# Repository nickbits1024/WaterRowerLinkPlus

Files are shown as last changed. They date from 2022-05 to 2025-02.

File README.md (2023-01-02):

# WaterRower Link+

## Description
WaterRower Link+ is a bluetooth module designed for any WaterRower with the S4 monitor.  It provides all the functionality of the official WaterRower ComModule as well as many additional features.

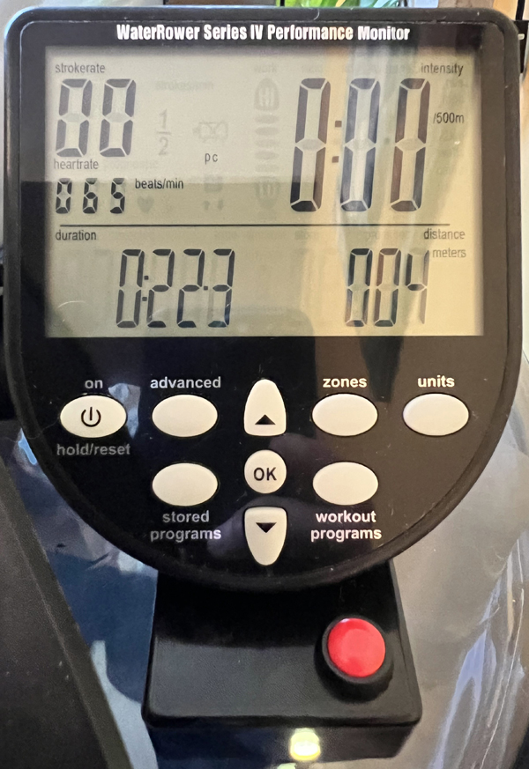
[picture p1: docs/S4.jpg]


## Features
- Replaces WaterRower ComModule and External ANT+ Module
  - External ANT+ connection Works on M1 when using recommended cable (unlike the official ANT+ Plugin-In module!)
- Bluetooth
  - Bluetooth Fitness Machine Profile
    - Rower Data
    - Indoor Bike Data
  - Supports BLE HRMs
- ANT+
  - Fitness Equipment Profile
  - Supports ANT+ HRMs
- S4 monitor heart rate provider
  - Sends captured ANT+/BLE HR data for display on S4 monitor
- ANT+ to BLE HRM bridge
  - WRL+ will broadcast ANT+ HR data over BLE for use in apps that only support BLE. e.g. SuperNatural

## Tested Software
- WaterRower Connect
- Holofit
- VZFit
- ZWift
- Garmin Fenix 6
- SuperNatural (HR only)

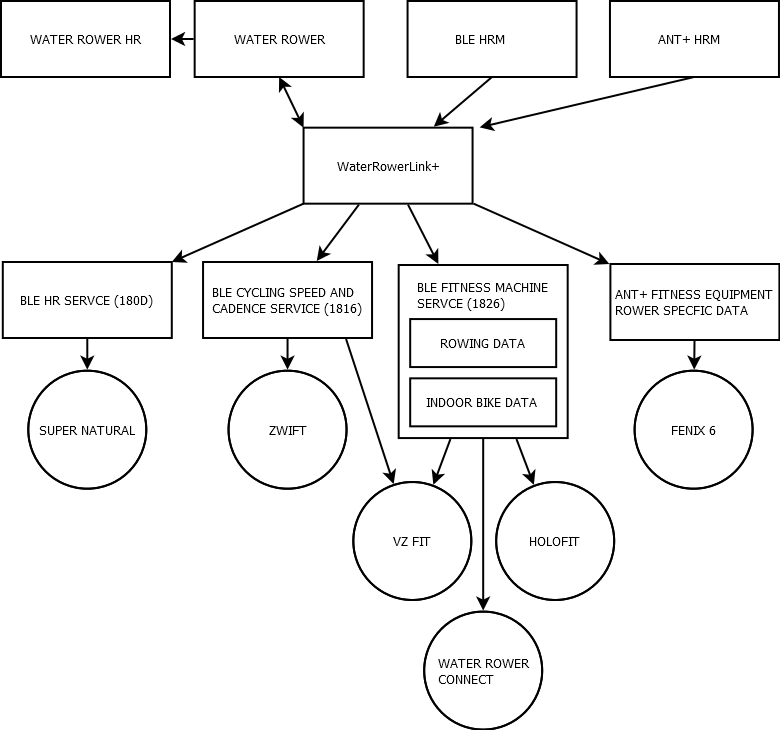
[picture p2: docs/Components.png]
Components


## Hardware
Hardware design is available in the KiCad projects in this repo.  There are two versions, [breadboard](hardware/breadboard/) and [PCB](hardware/pcb/).  With the breadboard version, everything can be assembled using dev boards and jumper wires. [^1]  Both solderless and soldered breadboards were tested and work.  The PCB version requires the design be sent to a PCB manufacturer.

### Soldered Breadboard Version
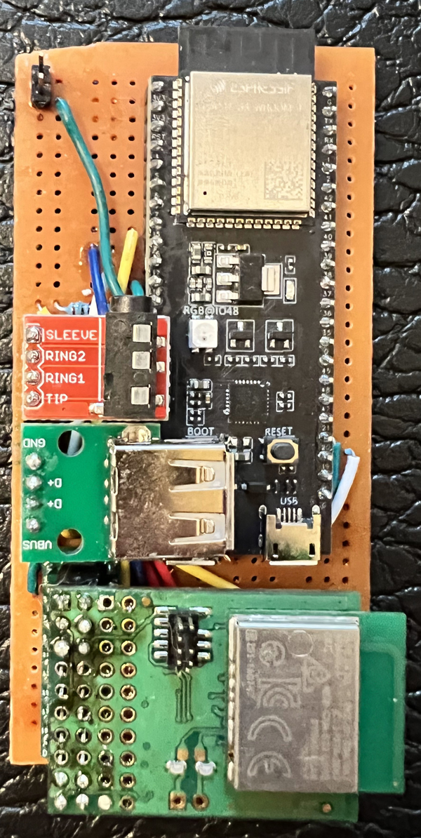
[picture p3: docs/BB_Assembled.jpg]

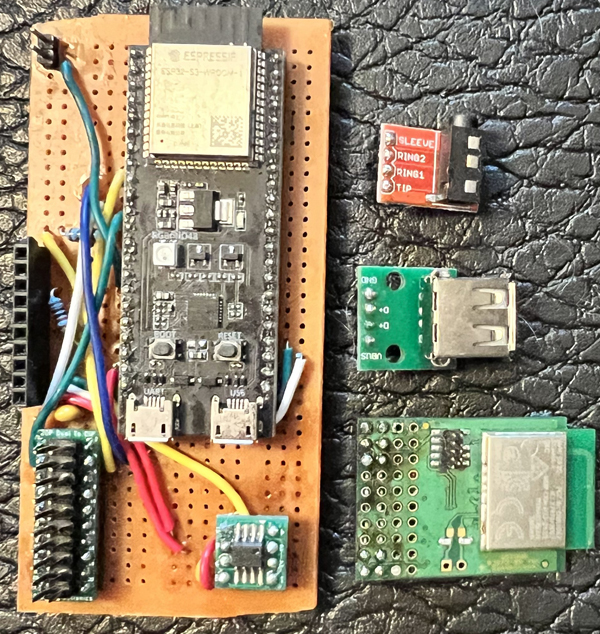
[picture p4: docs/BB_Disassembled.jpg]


### PCB Version
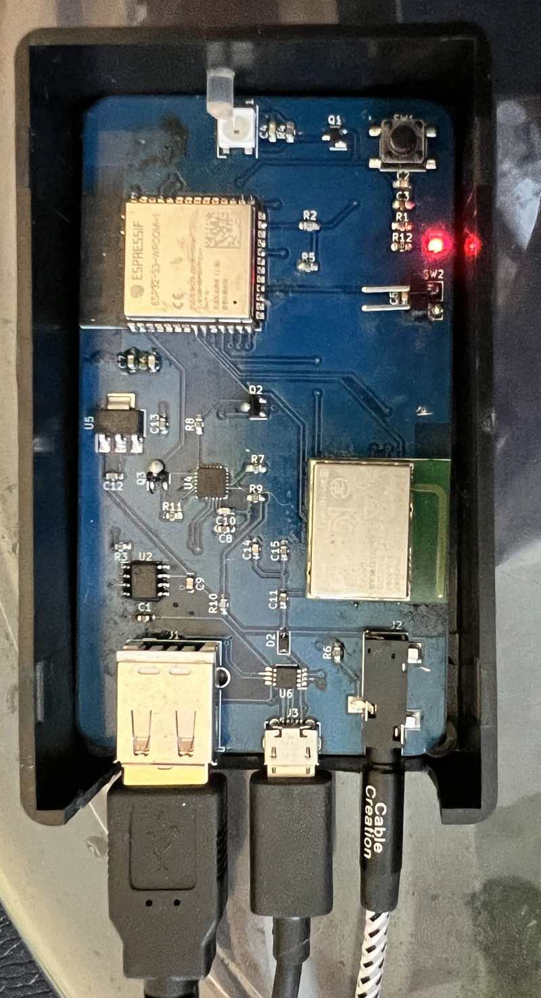
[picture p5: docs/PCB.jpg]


## Breadboard Bill of Materials
|Qty|Reference|Part|Foot Print|Supplier|
|---|---|----|---|---|
|1|C1|1uF|THT||[Amazon](https://www.amazon.com/gp/product/B085RDTCCV)
|1|C2|0.1uF|THT||(See above)
|1|J1|AudioPlug3|2.54mm|[Amazon](https://www.amazon.com/gp/product/B07L3P93ZD)
|1|J4|USB_A|2.54mm|[Amazon](https://www.amazon.com/gp/product/B07MBSTZYG)
|2|R1, R2|10k|THT|[Amazon](https://www.amazon.com/gp/product/B072BL2VX1)
|1|SW2|Button|12mm|[Amazon](https://www.amazon.com/gp/product/B07F8GBWGG)
|1|U1|ESP32-S3-DevKitC-1|DIP|[Amazon](https://www.amazon.com/gp/product/B09CPNRDND)
|1|U2|LM3525M-H|SOIC-8|[Mouser](https://www.mouser.com/ProductDetail/926-LM3525MX-H-NOPB)
|1|U2|SOIC-8 TO DIP||[Amazon](https://www.amazon.com/gp/product/B07CJ96ZPW)
|1|U3|D52QD2M6IA[^2]|2x10_2.54mm|[Digi-Key](https://www.digikey.com/en/products/detail/garmin-canada-inc/D52QD2M6IA-A-TRAY/6149453)
|1||PCB Breadboard|50x100|[Amazon](https://www.amazon.com/gp/product/B07ZP4FYVJ)
|1|Project Box|B07W78LN1V|100 x 60 x 25|[Amazon](https://www.amazon.com/gp/product/B07W78LN1V)
|1|TRS Cable|CC0377|3.5mm|[Amazon](https://www.amazon.com/gp/product/B01K3WXQDW)
|1|USB Cable|3896|Mini USB|[Monoprice](https://www.monoprice.com/product?p_id=3896)

## PCB Bill of Materials
|Qty|Reference|Part|Foot Print|Supplier|
|---|---|----|---|---|
|2|C1, C3|1uF cap|0603|[Amazon](https://www.amazon.com/gp/product/B06XDG3WQX)
|8|C2, C4, C5, C6, C9, C10, C14, C16|0.1uF cap|0603|(See above)
|2|C7, C11|C 10uF cap|0603|(See above)
|4|C8, C12, C13, C15|4.7uF cap|0603|(See above)
|1|D1|SK6812|5x5mm|[Digi-Key](https://www.digikey.com/en/products/detail/adafruit-industries-llc/1655/5154679)
|1|D2|1N5819|SOD-323|[Digi-Key](https://www.digikey.com/en/products/detail/micro-commercial-co/B5819WS-TP/2213555)
|1|D3|RED LED|0603|[Amazon](https://www.amazon.com/gp/product/B01CUGA380)
|1|J1|Molex_67643|USB-A|[Mouser](https://www.mouser.com/ProductDetail/538-67643-3910)
|1|J2|CUI_SJ-3523|3.5mm|[Mouser](https://www.mouser.com/ProductDetail/490-SJ-3523-SMT-TR)
|1|J3|Molex-105017-0001|Micro USB|[Mouser](https://www.mouser.com/ProductDetail/538-105017-0001)
|1|Q1|BSS138|SOT-23|[Mouser](https://www.mouser.com/ProductDetail/512-BSS138W)
|2|Q2, Q3|S8050|SOT-23|[Amazon](https://www.amazon.com/gp/product/B07KPCBP24)
|7|R1, R3, R4, R5, R6, R8, R11|10K res|0603|[Amazon](https://www.amazon.com/gp/product/B095P6L5PB)
|2|R2, R7|1K res|0603|(See above)
|1|R9|47K res|0603|(See above)
|1|R10|22K res|0603|(See above)
|1|R12|5.1K res|0603|(See above)
|1|SW2|Header|2x2.54mm|[Amazon](https://www.amazon.com/gp/product/B01461DQ6S) 
|1|SW2|Button|12mm|[Amazon](https://www.amazon.com/gp/product/B07F8GBWGG)
|1|SW4|RESET|2x2.54mm|(See above)
|1|SW1|RESET|6x6mm|[Amazon](https://www.amazon.com/gp/product/B077N3D7BD)
|1|SW3|BOOT|6x6mm|(See RESET)
|1|U1|ESP32-S3-WROOM-1|ESP32-S3-WROOM-1|[Mouser](https://www.mouser.com/ProductDetail/356-ESP32-S3WROOM1N8)
|1|U2|LM3525M-H|SOIC-8|[Mouser](https://www.mouser.com/ProductDetail/926-LM3525MX-H-NOPB)
|1|U3|D52Q|D52QD2M4IA|[Digi-Key](https://www.digikey.com/en/products/detail/garmin-canada-inc/D52QD2M4IA-TRAY/6149451)
|1|U4|CP2102N-Axx-xQFN24|QFN-24|[Digi-Key](https://www.digikey.com/en/products/detail/silicon-labs/CP2102N-A02-GQFN24/9863476)
|1|U5|AP7361C-33E|SOT-223|[Digi-Key](https://www.digikey.com/en/products/detail/diodes-incorporated/AP7361-33E-13/4249788)
|1|U6|SP0506BAATG|MSOP-8|[Mouser](https://www.mouser.com/ProductDetail/576-SP0506BAATG)
|1|Project Box|B07W78LN1V|100 x 60 x 25|[Amazon](https://www.amazon.com/gp/product/B07W78LN1V)
|1|TRS Cable|CC0377|3.5mm|[Amazon](https://www.amazon.com/gp/product/B01K3WXQDW)
|1|USB Cable|3896|Mini USB|[Monoprice](https://www.monoprice.com/product?p_id=3896)
|1|Light Pipe||RA|[Digi-Key](https://www.digikey.com/en/products/detail/dialight/51513620375F/9742144)

## Cable Connections
1. Attach mini USB cable to S4 monitor and WaterRower Link+
2. Attach 3.5mm cable to S4 monitor and WaterRower Link+.  The recommended cable will fit in the narrow gap of an M1 rower and the monitor.
2. Attach micro USB cable to USB power supply

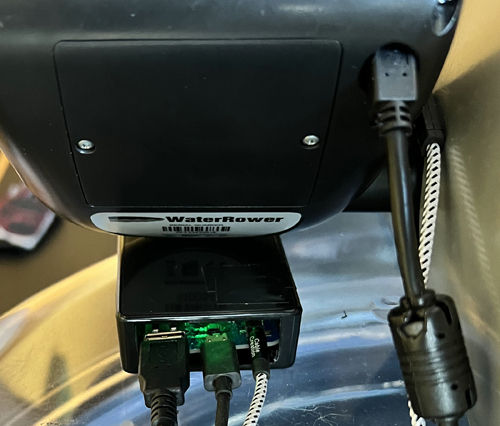
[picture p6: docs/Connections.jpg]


### Required Software
- [Visual Studio Code](https://code.visualstudio.com/download)
- [Visual Studio Code Espressif IDF extension](https://marketplace.visualstudio.com/items?itemName=espressif.esp-idf-extension)
- [ESP-IDF](https://dl.espressif.com/dl/esp-idf/) Built using commit 0132079fa51f2c130513dd634e97ef9726f00e85

### Equipment Used
- Soldering Iron: [YIHUA 995D+](https://www.amazon.com/gp/product/B0919MS875)
- PCB Hot Plate: [MINIWARE MHP30M Mini Hot Plate](https://www.amazon.com/gp/product/B08R6XFPKR)
- PCB Holder: [Stickvise](https://www.stickvise.com/)
- Microscope: [AMScope SM745NTP-B](https://amscope.com/products/sm745ntp-b) + [DAB](https://amscope.com/products/DAB)

## Usage
Once power is provided, a red LED will illuminate on the board and should be detectable in apps.  Press the button connected to SW2 turn on the S4 monitor.  The NeoPixel will illuminate green when it detects it over the USB connection.  It will power off automatically after 30 minutes of inactivity.  When WRL+ is receiving data from the S4, the LED will turn cyan. When it detects a heart rate over BLE or ANT+, it will beat red.
Note the software only supports one HRM.  If multiple are detected, only the first one seen will be connected.

## Known Issues
- The last update to VZfit displays HR in the HUD however the value does not appear correct.  It may be a bug with WRL+ or VZfit.

## Credits
This project was inspired by [PiRowFlow](https://github.com/inonoob/pirowflo)

[^1]: The LM3525M must be soldered to the SOIC-8 TO DIP first
[^2]: This part is EOL at Digi-Key.  I do not know if there is a compatible replacement.

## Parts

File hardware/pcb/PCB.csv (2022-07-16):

Source: | C:\Users\nickb\Documents\esp-idf\WaterRowerLinkPlus\hardware\PCB\PCB.kicad_sch
Date: | 7/16/2022 12:26:23 PM
Tool: | Eeschema (6.0.5)
Generator: | C:\Program Files\KiCad\6.0\bin\scripting\plugins/bom_csv_grouped_by_value.py
Component Count: | 47
Individual Components:
Item | Qty | Reference(s) | Value | LibPart | Footprint | Datasheet
 |  | C1 | 1uF | Device:C | Capacitor_SMD:C_0603_1608Metric_Pad1.08x0.95mm_HandSolder | ~
 |  | C2 | 0.1uF | Device:C | Capacitor_SMD:C_0603_1608Metric_Pad1.08x0.95mm_HandSolder | ~
 |  | C3 | 1uF | Device:C | Capacitor_SMD:C_0603_1608Metric_Pad1.08x0.95mm_HandSolder | ~
 |  | C4 | 0.1uF | Device:C | Capacitor_SMD:C_0603_1608Metric_Pad1.08x0.95mm_HandSolder | ~
 |  | C5 | 0.1uF | Device:C | Capacitor_SMD:C_0603_1608Metric_Pad1.08x0.95mm_HandSolder | ~
 |  | C6 | 0.1uF | Device:C | Capacitor_SMD:C_0603_1608Metric_Pad1.08x0.95mm_HandSolder | ~
 |  | C7 | 10uF | Device:C | Capacitor_SMD:C_0603_1608Metric_Pad1.08x0.95mm_HandSolder | ~
 |  | C8 | 4.7uF | Device:C | Capacitor_SMD:C_0603_1608Metric_Pad1.08x0.95mm_HandSolder | ~
 |  | C9 | 0.1uF | Device:C | Capacitor_SMD:C_0603_1608Metric_Pad1.08x0.95mm_HandSolder | ~
 |  | C10 | 0.1uF | Device:C | Capacitor_SMD:C_0603_1608Metric_Pad1.08x0.95mm_HandSolder | ~
 |  | C11 | 10uF | Device:C | Capacitor_SMD:C_0603_1608Metric_Pad1.08x0.95mm_HandSolder | ~
 |  | C12 | 4.7uF | Device:C | Capacitor_SMD:C_0603_1608Metric_Pad1.08x0.95mm_HandSolder | ~
 |  | C13 | 4.7uF | Device:C | Capacitor_SMD:C_0603_1608Metric_Pad1.08x0.95mm_HandSolder | ~
 |  | C14 | 0.1uF | Device:C | Capacitor_SMD:C_0603_1608Metric_Pad1.08x0.95mm_HandSolder | ~
 |  | C15 | 4.7uF | Device:C | Capacitor_SMD:C_0603_1608Metric_Pad1.08x0.95mm_HandSolder | ~
 |  | C16 | 0.1uF | Device:C | Capacitor_SMD:C_0603_1608Metric_Pad1.08x0.95mm_HandSolder | ~
 |  | D1 | SK6812 | LED:SK6812 | LED_SMD:LED_SK6812_PLCC4_5.0x5.0mm_P3.2mm | https://cdn-shop.adafruit.com/product-files/1138/SK6812+LED+datasheet+.pdf
 |  | D2 | 1N5819 | Diode:1N5819 | Diode_SMD:D_SOD-323_HandSoldering | http://www.vishay.com/docs/88525/1n5817.pdf
 |  | D3 | RED LED | Device:LED | Capacitor_SMD:C_0603_1608Metric_Pad1.08x0.95mm_HandSolder | ~
 |  | J1 | USB_A | Connector:USB_A | Connector_USB:USB_A_Molex_67643_Horizontal | ~
 |  | J2 | AudioJack3 | Connector:AudioJack3 | Connector_Audio:Jack_3.5mm_CUI_SJ-3523-SMT_Horizontal | ~
 |  | J3 | USB_B_Micro | Connector:USB_B_Micro | Connector_USB:USB_Micro-B_Molex-105017-0001 | ~
 |  | Q1 | BSS138 | Transistor_FET:BSS138 | Package_TO_SOT_SMD:SOT-23 | https://www.onsemi.com/pub/Collateral/BSS138-D.PDF
 |  | Q2 | MMBT3904 | Transistor_BJT:MMBT3904 | Package_TO_SOT_SMD:SOT-23 | https://www.onsemi.com/pub/Collateral/2N3903-D.PDF
 |  | Q3 | MMBT3904 | Transistor_BJT:MMBT3904 | Package_TO_SOT_SMD:SOT-23 | https://www.onsemi.com/pub/Collateral/2N3903-D.PDF
 |  | R1 | 10K | Device:R | Resistor_SMD:R_0603_1608Metric_Pad0.98x0.95mm_HandSolder | ~
 |  | R2 | 1K | Device:R | Resistor_SMD:R_0603_1608Metric_Pad0.98x0.95mm_HandSolder | ~
 |  | R3 | 10K | Device:R | Resistor_SMD:R_0603_1608Metric_Pad0.98x0.95mm_HandSolder | ~
 |  | R4 | 10K | Device:R | Resistor_SMD:R_0603_1608Metric_Pad0.98x0.95mm_HandSolder | ~
 |  | R5 | 10K | Device:R | Resistor_SMD:R_0603_1608Metric_Pad0.98x0.95mm_HandSolder | ~
 |  | R6 | 10K | Device:R | Resistor_SMD:R_0603_1608Metric_Pad0.98x0.95mm_HandSolder | ~
 |  | R7 | 1K | Device:R | Resistor_SMD:R_0603_1608Metric_Pad0.98x0.95mm_HandSolder | ~
 |  | R8 | 10K | Device:R | Resistor_SMD:R_0603_1608Metric_Pad0.98x0.95mm_HandSolder | ~
 |  | R9 | 47K | Device:R | Resistor_SMD:R_0603_1608Metric_Pad0.98x0.95mm_HandSolder | ~
 |  | R10 | 22K | Device:R | Resistor_SMD:R_0603_1608Metric_Pad0.98x0.95mm_HandSolder | ~
 |  | R11 | 10K | Device:R | Resistor_SMD:R_0603_1608Metric_Pad0.98x0.95mm_HandSolder | ~
 |  | R12 | 5.1K | Device:R | Resistor_SMD:R_0603_1608Metric_Pad0.98x0.95mm_HandSolder | ~
 |  | SW1 | RESET | Switch:SW_Push | Button_Switch_SMD:SW_Push_1P1T_NO_6x6mm_H9.5mm | ~
 |  | SW2 | S4 | Switch:SW_Push | Connector_PinHeader_2.54mm:PinHeader_1x02_P2.54mm_Vertical | ~
 |  | SW3 | BOOT | Switch:SW_Push | Button_Switch_SMD:SW_Push_1P1T_NO_6x6mm_H9.5mm | ~
 |  | SW4 | RESET | Switch:SW_Push | Connector_PinHeader_2.54mm:PinHeader_1x02_P2.54mm_Vertical | ~
 |  | U1 | ESP32-S3-WROOM-1 | Espressif:ESP32-S3-WROOM-1 | Espressif:ESP32-S3-WROOM-1
 |  | U2 | LM3525M-H | MyParts:LM3525M-H | Package_SO:SOIC-8_3.9x4.9mm_P1.27mm
 |  | U3 | D52Q | MyParts:D52Q | MyParts:D52Q
 |  | U4 | CP2102N-Axx-xQFN24 | Interface_USB:CP2102N-Axx-xQFN24 | Package_DFN_QFN:QFN-24-1EP_4x4mm_P0.5mm_EP2.6x2.6mm | https://www.silabs.com/documents/public/data-sheets/cp2102n-datasheet.pdf
 |  | U5 | AP7361C-33E | Regulator_Linear:AP7361C-33E | Package_TO_SOT_SMD:SOT-223 | https://www.diodes.com/assets/Datasheets/AP7361C.pdf
 |  | U6 | SP0506BAATG | MyParts:SP0506BAATG | Package_SO:MSOP-8_3x3mm_P0.65mm
Collated Components:
Item | Qty | Reference(s) | Value | LibPart | Footprint | Datasheet
1 | 2 | C1, C3 | 1uF | Device:C | Capacitor_SMD:C_0603_1608Metric_Pad1.08x0.95mm_HandSolder | ~
2 | 8 | C2, C4, C5, C6, C9, C10, C14, C16 | 0.1uF | Device:C | Capacitor_SMD:C_0603_1608Metric_Pad1.08x0.95mm_HandSolder | ~
3 | 2 | C7, C11 | 10uF | Device:C | Capacitor_SMD:C_0603_1608Metric_Pad1.08x0.95mm_HandSolder | ~
4 | 4 | C8, C12, C13, C15 | 4.7uF | Device:C | Capacitor_SMD:C_0603_1608Metric_Pad1.08x0.95mm_HandSolder | ~
5 | 1 | D1 | SK6812 | LED:SK6812 | LED_SMD:LED_SK6812_PLCC4_5.0x5.0mm_P3.2mm | https://cdn-shop.adafruit.com/product-files/1138/SK6812+LED+datasheet+.pdf
6 | 1 | D2 | 1N5819 | Diode:1N5819 | Diode_SMD:D_SOD-323_HandSoldering | http://www.vishay.com/docs/88525/1n5817.pdf
7 | 1 | D3 | RED LED | Device:LED | Capacitor_SMD:C_0603_1608Metric_Pad1.08x0.95mm_HandSolder | ~
8 | 1 | J1 | USB_A | Connector:USB_A | Connector_USB:USB_A_Molex_67643_Horizontal | ~
9 | 1 | J2 | AudioJack3 | Connector:AudioJack3 | Connector_Audio:Jack_3.5mm_CUI_SJ-3523-SMT_Horizontal | ~
10 | 1 | J3 | USB_B_Micro | Connector:USB_B_Micro | Connector_USB:USB_Micro-B_Molex-105017-0001 | ~
11 | 1 | Q1 | BSS138 | Transistor_FET:BSS138 | Package_TO_SOT_SMD:SOT-23 | https://www.onsemi.com/pub/Collateral/BSS138-D.PDF
12 | 2 | Q2, Q3 | MMBT3904 | Transistor_BJT:MMBT3904 | Package_TO_SOT_SMD:SOT-23 | https://www.onsemi.com/pub/Collateral/2N3903-D.PDF
13 | 7 | R1, R3, R4, R5, R6, R8, R11 | 10K | Device:R | Resistor_SMD:R_0603_1608Metric_Pad0.98x0.95mm_HandSolder | ~
14 | 2 | R2, R7 | 1K | Device:R | Resistor_SMD:R_0603_1608Metric_Pad0.98x0.95mm_HandSolder | ~
15 | 1 | R9 | 47K | Device:R | Resistor_SMD:R_0603_1608Metric_Pad0.98x0.95mm_HandSolder | ~
16 | 1 | R10 | 22K | Device:R | Resistor_SMD:R_0603_1608Metric_Pad0.98x0.95mm_HandSolder | ~
17 | 1 | R12 | 5.1K | Device:R | Resistor_SMD:R_0603_1608Metric_Pad0.98x0.95mm_HandSolder | ~
18 | 1 | SW1 | RESET | Switch:SW_Push | Button_Switch_SMD:SW_Push_1P1T_NO_6x6mm_H9.5mm | ~
19 | 1 | SW2 | S4 | Switch:SW_Push | Connector_PinHeader_2.54mm:PinHeader_1x02_P2.54mm_Vertical | ~
20 | 1 | SW3 | BOOT | Switch:SW_Push | Button_Switch_SMD:SW_Push_1P1T_NO_6x6mm_H9.5mm | ~
21 | 1 | SW4 | RESET | Switch:SW_Push | Connector_PinHeader_2.54mm:PinHeader_1x02_P2.54mm_Vertical | ~
22 | 1 | U1 | ESP32-S3-WROOM-1 | Espressif:ESP32-S3-WROOM-1 | Espressif:ESP32-S3-WROOM-1
23 | 1 | U2 | LM3525M-H | MyParts:LM3525M-H | Package_SO:SOIC-8_3.9x4.9mm_P1.27mm
24 | 1 | U3 | D52Q | MyParts:D52Q | MyParts:D52Q
25 | 1 | U4 | CP2102N-Axx-xQFN24 | Interface_USB:CP2102N-Axx-xQFN24 | Package_DFN_QFN:QFN-24-1EP_4x4mm_P0.5mm_EP2.6x2.6mm | https://www.silabs.com/documents/public/data-sheets/cp2102n-datasheet.pdf
26 | 1 | U5 | AP7361C-33E | Regulator_Linear:AP7361C-33E | Package_TO_SOT_SMD:SOT-223 | https://www.diodes.com/assets/Datasheets/AP7361C.pdf
27 | 1 | U6 | SP0506BAATG | MyParts:SP0506BAATG | Package_SO:MSOP-8_3x3mm_P0.65mm

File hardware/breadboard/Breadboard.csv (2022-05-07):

Source: | C:\Users\nickb\Documents\esp-idf\WaterRowerLinkPlus\hardware\breadboard\Breadboard.kicad_sch
Date: | 5/6/2022 6:08:07 PM
Tool: | Eeschema (6.0.1)
Generator: | C:\Program Files\KiCad\6.0\bin\scripting\plugins/bom_csv_grouped_by_value.py
Component Count: | 12
Individual Components:
Item | Qty | Reference(s) | Value | LibPart | Footprint | Datasheet
 |  | C1 | 1uF | Device:C | Capacitor_THT:C_Disc_D5.0mm_W2.5mm_P5.00mm | ~
 |  | C2 | 0.1uF | Device:C | Capacitor_THT:C_Disc_D5.0mm_W2.5mm_P5.00mm | ~
 |  | J1 | AudioPlug3 | Connector:AudioPlug3 |  | ~
 |  | J2 | Conn_01x04_Male | Connector:Conn_01x04_Male |  | ~
 |  | J3 | Conn_01x04_Female | Connector:Conn_01x04_Female | Connector_PinHeader_2.54mm:PinHeader_1x04_P2.54mm_Vertical | ~
 |  | J4 | USB_A | Connector:USB_A |  | ~
 |  | R1 | 10k | Device:R | Resistor_THT:R_Box_L13.0mm_W4.0mm_P9.00mm | ~
 |  | R2 | 10k | Device:R | Resistor_THT:R_Box_L13.0mm_W4.0mm_P9.00mm | ~
 |  | SW1 | SW_Push | Switch:SW_Push | Connector_PinHeader_2.54mm:PinHeader_1x02_P2.54mm_Vertical | ~
 |  | U1 | ESP32-S3-DevKitC-1 | MyParts:ESP32-S3-DevKitC-1 | MyParts:ESP32_S3_DevKitC-1
 |  | U2 | LM3525M-H | MyParts:LM3525M-H | Package_DIP:DIP-8_W7.62mm
 |  | U3 | D52QD2M6IA | MyParts:D52QD2M6IA | Connector_PinHeader_2.54mm:PinHeader_2x10_P2.54mm_Vertical
Collated Components:
Item | Qty | Reference(s) | Value | LibPart | Footprint | Datasheet
1 | 1 | C1 | 1uF | Device:C | Capacitor_THT:C_Disc_D5.0mm_W2.5mm_P5.00mm | ~
2 | 1 | C2 | 0.1uF | Device:C | Capacitor_THT:C_Disc_D5.0mm_W2.5mm_P5.00mm | ~
3 | 1 | J1 | AudioPlug3 | Connector:AudioPlug3 |  | ~
4 | 1 | J2 | Conn_01x04_Male | Connector:Conn_01x04_Male |  | ~
5 | 1 | J3 | Conn_01x04_Female | Connector:Conn_01x04_Female | Connector_PinHeader_2.54mm:PinHeader_1x04_P2.54mm_Vertical | ~
6 | 1 | J4 | USB_A | Connector:USB_A |  | ~
7 | 2 | R1, R2 | 10k | Device:R | Resistor_THT:R_Box_L13.0mm_W4.0mm_P9.00mm | ~
8 | 1 | SW1 | SW_Push | Switch:SW_Push | Connector_PinHeader_2.54mm:PinHeader_1x02_P2.54mm_Vertical | ~
9 | 1 | U1 | ESP32-S3-DevKitC-1 | MyParts:ESP32-S3-DevKitC-1 | MyParts:ESP32_S3_DevKitC-1
10 | 1 | U2 | LM3525M-H | MyParts:LM3525M-H | Package_DIP:DIP-8_W7.62mm
11 | 1 | U3 | D52QD2M6IA | MyParts:D52QD2M6IA | Connector_PinHeader_2.54mm:PinHeader_2x10_P2.54mm_Vertical

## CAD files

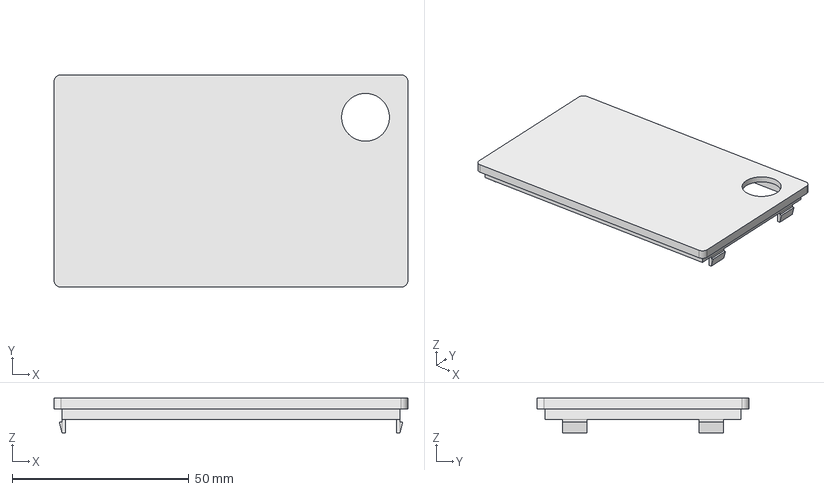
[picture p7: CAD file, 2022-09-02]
case/Cover.step
100.0 x 60.0 x 9.75 mm

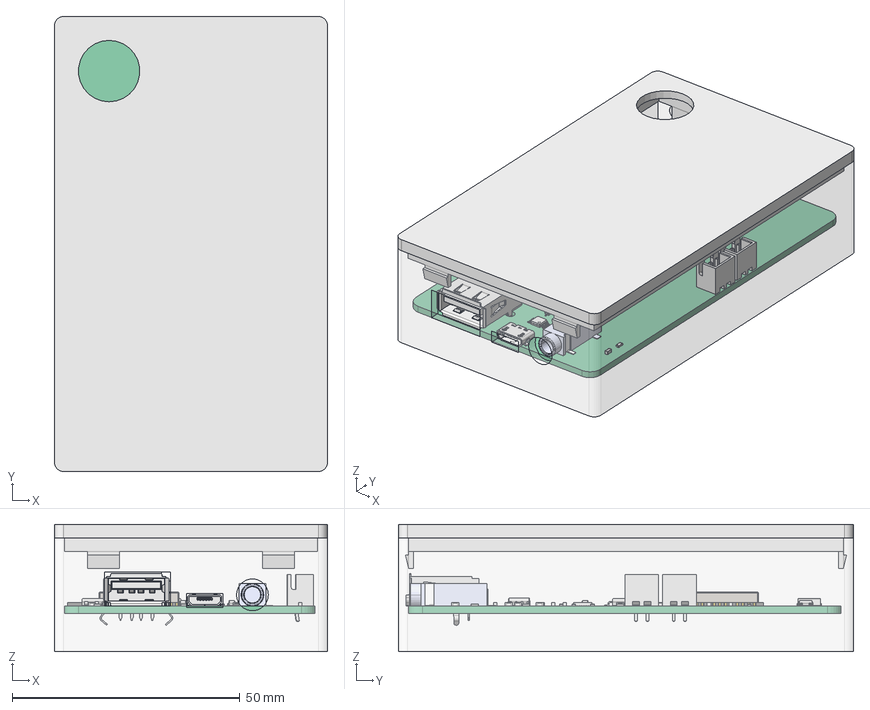
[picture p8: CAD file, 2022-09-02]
case/WaterRower Link Plus.FCStd
60.0 x 100.0 x 28.0 mm
Cover
Pcb_6ed7
D3_C_0603_1608Metric_a32fcbbb49ce
D3_C_0603_1608Metric_a32fcbbb49ce001
D3_C_0603_1608Metric_a32fcbbb49ce002
Q2_SOT_23_1edc0d5d0bdf
D3_C_0603_1608Metric_a32fcbbb49ce003
SW4_JST_B2B_XH_A_e1ea7425747a
R10_R_0603_1608Metric_ceb84cfbe445
D3_C_0603_1608Metric_a32fcbbb49ce004
R10_R_0603_1608Metric_ceb84cfbe446
R10_R_0603_1608Metric_ceb84cfbe447
D3_C_0603_1608Metric_a32fcbbb49ce005
D3_C_0603_1608Metric_a32fcbbb49ce006
U6_MSOP_8_3x3mm_P065mm_2c49078cca31
R10_R_0603_1608Metric_ceb84cfbe448
D2_D_SOD_323_26d3eac8a00f
U5_SOT_223_bfa9d087ecb1
U4_QFN-24-1EP_4x4mm_Pitch0.5mm_67e6553716d0
D3_C_0603_1608Metric_a32fcbbb49ce007
R10_R_0603_1608Metric_ceb84cfbe449
R10_R_0603_1608Metric_ceb84cfbe450
D3_C_0603_1608Metric_a32fcbbb49ce008
D3_C_0603_1608Metric_a32fcbbb49ce009
C0201_20210301.STEP^C0201_20210301.STEP_Submodel-C0201_part_ DesignRootModel_PCB_ESP32-S3-WROOM-1_V1(2)_PCB_ESP32-S3-WROOM-1_V1
L0201_20210301.STEP^L0201_20210301.STEP_Submodel-L0201_part_ DesignRootModel_PCB_ESP32-S3-WROOM-1_V1(2)_PCB_ESP32-S3-WROOM-1_V1
C0402_20210301.STEP^C0402_20210301.STEP_Submodel-C0402_part_ DesignRootModel_PCB_ESP32-S3-WROOM-1_V1(2)_PCB_ESP32-S3-WROOM-1_V1
R0201_20210301.STEP^R0201_20210301.STEP_Submodel-R0201_part_ DesignRootModel_PCB_ESP32-S3-WROOM-1_V1(2)_PCB_ESP32-S3-WROOM-1_V1
R0201_20210301.STEP^R0201_20210301.STEP_Submodel-R0201_part_ DesignRootModel_PCB_ESP32-S3-WROOM-1_V1(2)_PCB_ESP32-S3-WROOM-1_V002
R0201_20210301.STEP^R0201_20210301.STEP_Submodel-R0201_part_ DesignRootModel_PCB_ESP32-S3-WROOM-1_V1(2)_PCB_ESP32-S3-WROOM-1_V003
R0201_20210301.STEP^R0201_20210301.STEP_Submodel-R0201_part_ DesignRootModel_PCB_ESP32-S3-WROOM-1_V1(2)_PCB_ESP32-S3-WROOM-1_V005
R0201_20210301.STEP^R0201_20210301.STEP_Submodel-R0201_part_ DesignRootModel_PCB_ESP32-S3-WROOM-1_V1(2)_PCB_ESP32-S3-WROOM-1_V006
R0201_20210301.STEP^R0201_20210301.STEP_Submodel-R0201_part_ DesignRootModel_PCB_ESP32-S3-WROOM-1_V1(2)_PCB_ESP32-S3-WROOM-1_V007
R0201_20210301.STEP^R0201_20210301.STEP_Submodel-R0201_part_ DesignRootModel_PCB_ESP32-S3-WROOM-1_V1(2)_PCB_ESP32-S3-WROOM-1_V009
R0201_20210301.STEP^R0201_20210301.STEP_Submodel-R0201_part_ DesignRootModel_PCB_ESP32-S3-WROOM-1_V1(2)_PCB_ESP32-S3-WROOM-1_V010
R0201_20210301.STEP^R0201_20210301.STEP_Submodel-R0201_part_ DesignRootModel_PCB_ESP32-S3-WROOM-1_V1(2)_PCB_ESP32-S3-WROOM-1_V011
R0201_20210301.STEP^R0201_20210301.STEP_Submodel-R0201_part_ DesignRootModel_PCB_ESP32-S3-WROOM-1_V1(2)_PCB_ESP32-S3-WROOM-1_V013
R0201_20210301.STEP^R0201_20210301.STEP_Submodel-R0201_part_ DesignRootModel_PCB_ESP32-S3-WROOM-1_V1(2)_PCB_ESP32-S3-WROOM-1_V014
R0201_20210301.STEP^R0201_20210301.STEP_Submodel-R0201_part_ DesignRootModel_PCB_ESP32-S3-WROOM-1_V1(2)_PCB_ESP32-S3-WROOM-1_V015
R0201_20210301.STEP^R0201_20210301.STEP_Submodel-R0201_part_ DesignRootModel_PCB_ESP32-S3-WROOM-1_V1(2)_PCB_ESP32-S3-WROOM-1_V017
R0201_20210301.STEP^R0201_20210301.STEP_Submodel-R0201_part_ DesignRootModel_PCB_ESP32-S3-WROOM-1_V1(2)_PCB_ESP32-S3-WROOM-1_V018
R0201_20210301.STEP^R0201_20210301.STEP_Submodel-R0201_part_ DesignRootModel_PCB_ESP32-S3-WROOM-1_V1(2)_PCB_ESP32-S3-WROOM-1_V019
R0201_20210301.STEP^R0201_20210301.STEP_Submodel-R0201_part_ DesignRootModel_PCB_ESP32-S3-WROOM-1_V1(2)_PCB_ESP32-S3-WROOM-1_V021
R0201_20210301.STEP^R0201_20210301.STEP_Submodel-R0201_part_ DesignRootModel_PCB_ESP32-S3-WROOM-1_V1(2)_PCB_ESP32-S3-WROOM-1_V022
R0201_20210301.STEP^R0201_20210301.STEP_Submodel-R0201_part_ DesignRootModel_PCB_ESP32-S3-WROOM-1_V1(2)_PCB_ESP32-S3-WROOM-1_V023
R0201_20210301.STEP^R0201_20210301.STEP_Submodel-R0201_part_ DesignRootModel_PCB_ESP32-S3-WROOM-1_V1(2)_PCB_ESP32-S3-WROOM-1_V025
R0201_20210301.STEP^R0201_20210301.STEP_Submodel-R0201_part_ DesignRootModel_PCB_ESP32-S3-WROOM-1_V1(2)_PCB_ESP32-S3-WROOM-1_V026
R0201_20210301.STEP^R0201_20210301.STEP_Submodel-R0201_part_ DesignRootModel_PCB_ESP32-S3-WROOM-1_V1(2)_PCB_ESP32-S3-WROOM-1_V027
R0201_20210301.STEP^R0201_20210301.STEP_Submodel-R0201_part_ DesignRootModel_PCB_ESP32-S3-WROOM-1_V1(2)_PCB_ESP32-S3-WROOM-1_V029
R0201_20210301.STEP^R0201_20210301.STEP_Submodel-R0201_part_ DesignRootModel_PCB_ESP32-S3-WROOM-1_V1(2)_PCB_ESP32-S3-WROOM-1_V030
R0201_20210301.STEP^R0201_20210301.STEP_Submodel-R0201_part_ DesignRootModel_PCB_ESP32-S3-WROOM-1_V1(2)_PCB_ESP32-S3-WROOM-1_V031
L0201_20210301.STEP^L0201_20210301.STEP_Submodel-L0201_part_ DesignRootModel_PCB_ESP32-S3-WROOM-1_V1(2)_PCB_ESP32-S3-WROOM-1_V002
L0201_20210301.STEP^L0201_20210301.STEP_Submodel-L0201_part_ DesignRootModel_PCB_ESP32-S3-WROOM-1_V1(2)_PCB_ESP32-S3-WROOM-1_V003
C0201_20210301.STEP^C0201_20210301.STEP_Submodel-C0201_part_ DesignRootModel_PCB_ESP32-S3-WROOM-1_V1(2)_PCB_ESP32-S3-WROOM-1_V002
C0201_20210301.STEP^C0201_20210301.STEP_Submodel-C0201_part_ DesignRootModel_PCB_ESP32-S3-WROOM-1_V1(2)_PCB_ESP32-S3-WROOM-1_V003
C0201_20210301.STEP^C0201_20210301.STEP_Submodel-C0201_part_ DesignRootModel_PCB_ESP32-S3-WROOM-1_V1(2)_PCB_ESP32-S3-WROOM-1_V004
C0201_20210301.STEP^C0201_20210301.STEP_Submodel-C0201_part_ DesignRootModel_PCB_ESP32-S3-WROOM-1_V1(2)_PCB_ESP32-S3-WROOM-1_V005
C0201_20210301.STEP^C0201_20210301.STEP_Submodel-C0201_part_ DesignRootModel_PCB_ESP32-S3-WROOM-1_V1(2)_PCB_ESP32-S3-WROOM-1_V006
C0201_20210301.STEP^C0201_20210301.STEP_Submodel-C0201_part_ DesignRootModel_PCB_ESP32-S3-WROOM-1_V1(2)_PCB_ESP32-S3-WROOM-1_V007
C0201_20210301.STEP^C0201_20210301.STEP_Submodel-C0201_part_ DesignRootModel_PCB_ESP32-S3-WROOM-1_V1(2)_PCB_ESP32-S3-WROOM-1_V008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

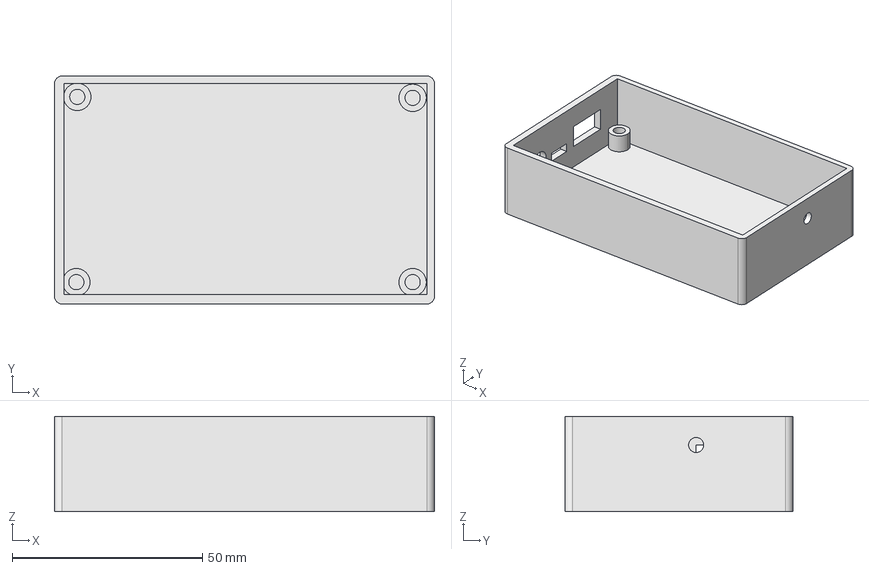
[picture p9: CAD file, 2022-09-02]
case/Box.step
100.0 x 60.0 x 25.0 mm

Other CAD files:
case/WaterRower Link Plus.3mf

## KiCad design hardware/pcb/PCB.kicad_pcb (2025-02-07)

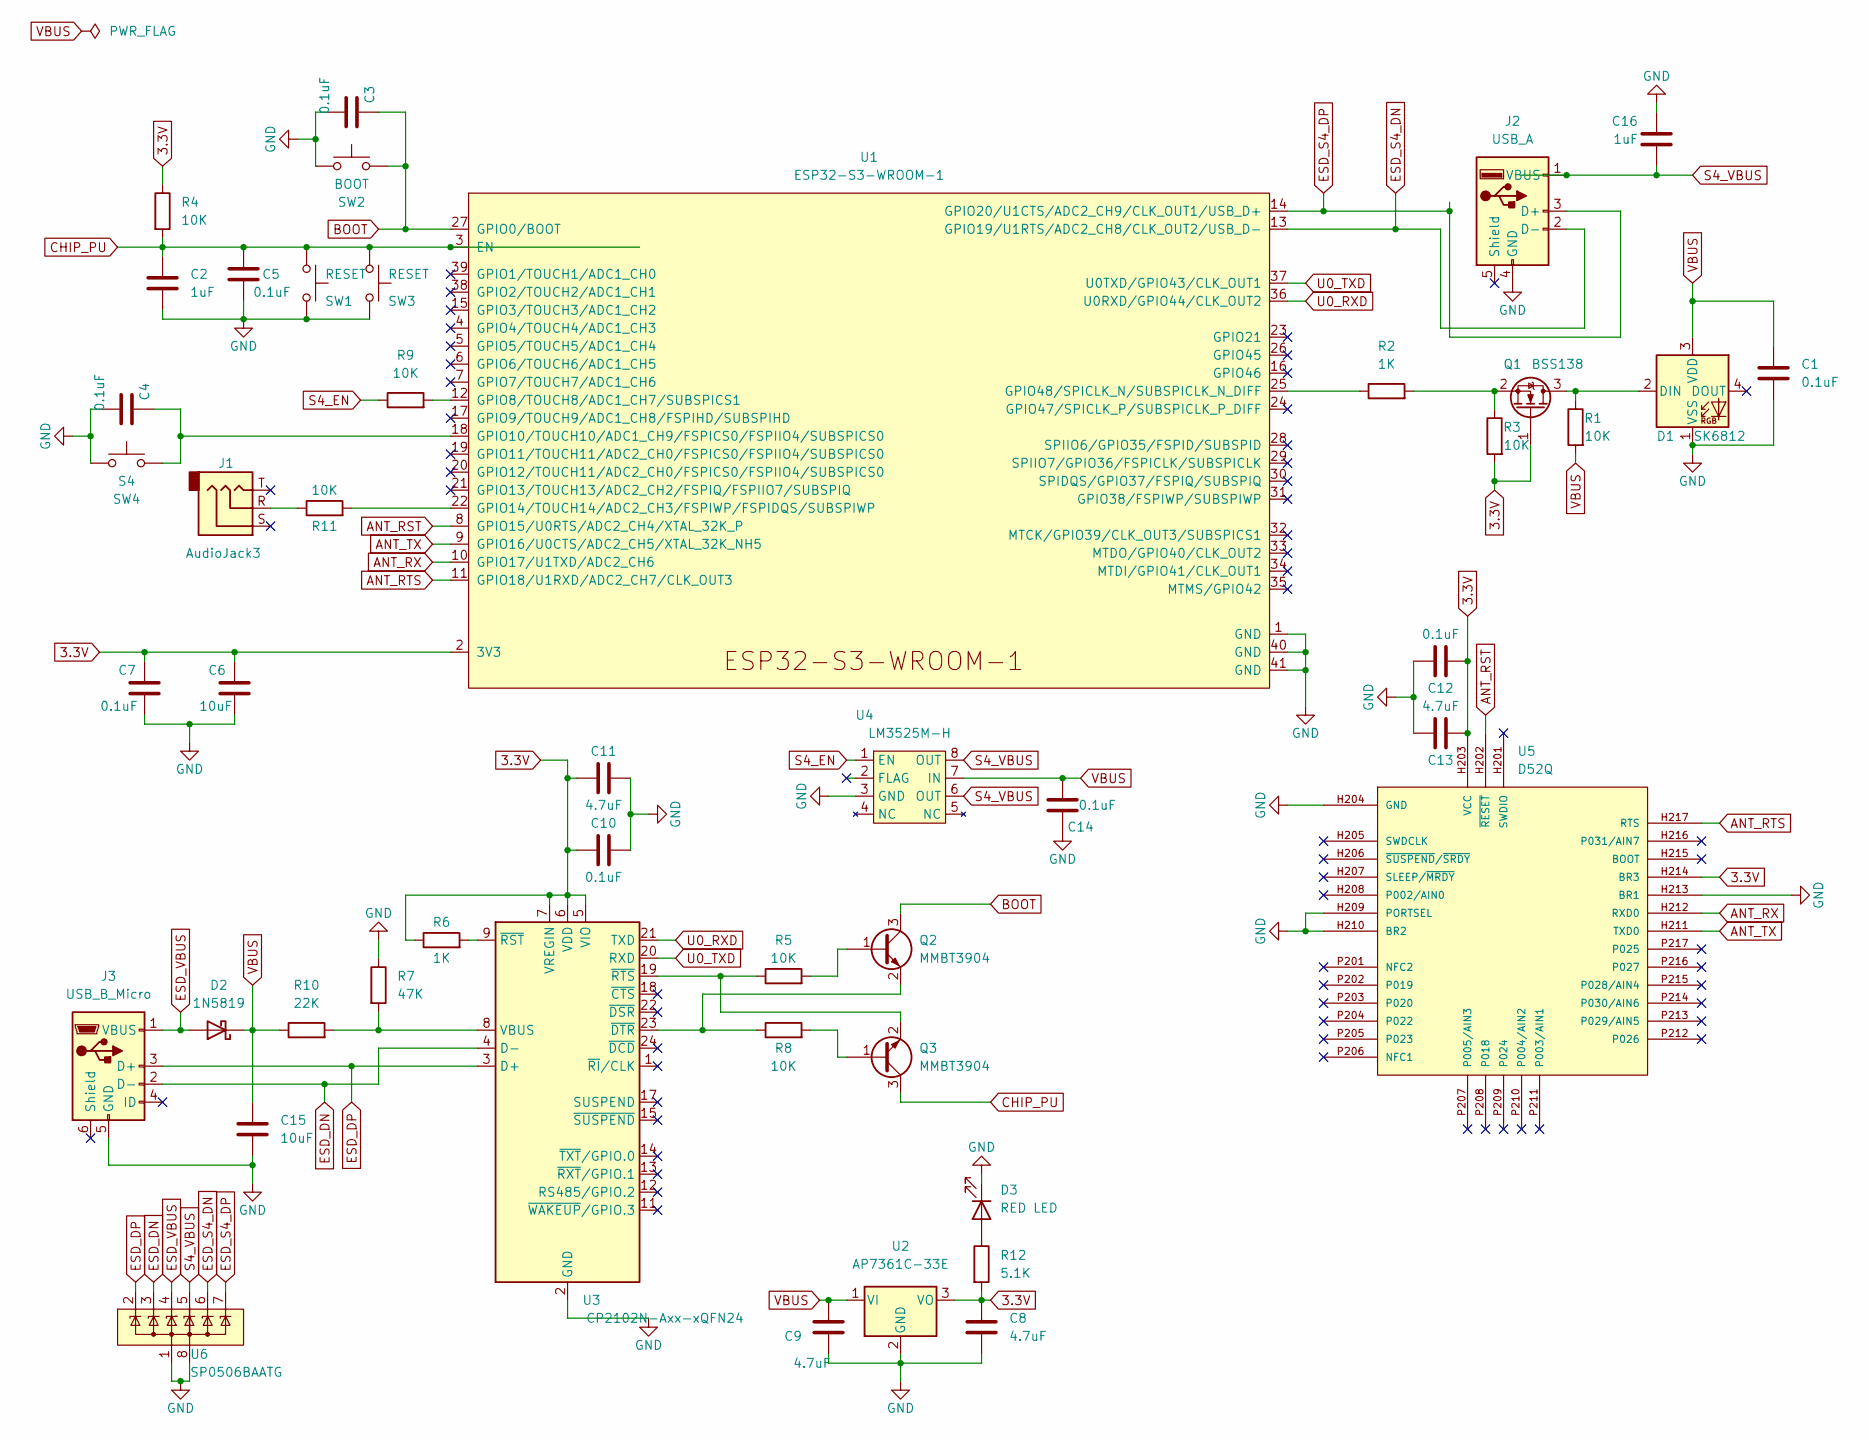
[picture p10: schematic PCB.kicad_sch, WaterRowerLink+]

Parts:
C1, C3, C4, C5, C7, C10, C12, C14: 0.1uF; C_0603_1608Metric_Pad1.08x0.95mm_HandSolder
C2, C16: 1uF; C_0603_1608Metric_Pad1.08x0.95mm_HandSolder
C6, C15: 10uF; C_0603_1608Metric_Pad1.08x0.95mm_HandSolder
C8, C9, C11, C13: 4.7uF; C_0603_1608Metric_Pad1.08x0.95mm_HandSolder
D1: SK6812; LED_SK6812_PLCC4_5.0x5.0mm_P3.2mm
D2: 1N5819; D_SOD-323_HandSoldering
D3: RED LED; LED_0603_1608Metric_Pad1.05x0.95mm_HandSolder
J1: AudioJack3; Jack_3.5mm_CUI_SJ-3523-SMT_Horizontal
J2: USB_A; USB_A_Molex_67643_Horizontal
J3: USB_B_Micro; USB_Micro-B_Molex-105017-0001
Q1: BSS138; SOT-23
Q2, Q3: MMBT3904; SOT-23
R1, R3, R4, R5, R8, R9, R11: 10K; R_0603_1608Metric_Pad0.98x0.95mm_HandSolder
R2, R6: 1K; R_0603_1608Metric_Pad0.98x0.95mm_HandSolder
R7: 47K; R_0603_1608Metric_Pad0.98x0.95mm_HandSolder
R10: 22K; R_0603_1608Metric_Pad0.98x0.95mm_HandSolder
R12: 5.1K; R_0603_1608Metric_Pad0.98x0.95mm_HandSolder
SW1: RESET; SW_Push_1P1T_NO_6x6mm_H9.5mm
SW2: BOOT; SW_Push_1P1T_NO_6x6mm_H9.5mm
SW3: RESET; JST_XH_B2B-XH-A_1x02_P2.50mm_Vertical
SW4: S4; JST_XH_B2B-XH-A_1x02_P2.50mm_Vertical
U1: ESP32-S3-WROOM-1
U2: AP7361C-33E; SOT-223
U3: CP2102N-Axx-xQFN24; QFN-24-1EP_4x4mm_P0.5mm_EP2.6x2.6mm
U4: LM3525M-H; SOIC-8_3.9x4.9mm_P1.27mm
U5: D52Q
U6: SP0506BAATG; MSOP-8_3x3mm_P0.65mm

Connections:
3.3V: C6.1, C7.1, C8.2, C10.1, C11.1, C12.1, C13.1, Q1.1 (G), R3.2, R4.1, R6.1, R12.2, U1.2 (3V3), U2.3 (VO), U3.5 (VIO), U3.6 (VDD), U3.7 (VREGIN), U5.H203 (VCC), U5.H214 (BR3)
ANT_RST: U1.8 (GPIO15/U0RTS/ADC2_CH4/XTAL_32K_P), U5.H202 (~RESET)
ANT_RTS: U1.11 (GPIO18/U1RXD/ADC2_CH7/CLK_OUT3), U5.H217 (RTS)
ANT_RX: U1.10 (GPIO17/U1TXD/ADC2_CH6), U5.H212 (RXD0)
ANT_TX: U1.9 (GPIO16/U0CTS/ADC2_CH5/XTAL_32K_NH5), U5.H211 (TXD0)
BOOT: C3.1, Q2.3 (C), SW2.2, U1.27 (GPIO0/BOOT)
CHIP_PU: C2.1, C5.2, Q3.3 (C), R4.2, SW1.2, SW3.2, U1.3 (EN)
ESD_DN: J3.2 (D-), U3.4 (D-), U6.3
ESD_DP: J3.3 (D+), U3.3 (D+), U6.2
ESD_S4_DN: J2.2 (D-), U1.13 (GPIO19/U1RTS/ADC2_CH8/CLK_OUT2/USB_D-), U6.6
ESD_S4_DP: J2.3 (D+), U1.14 (GPIO20/U1CTS/ADC2_CH9/CLK_OUT1/USB_D+), U6.7
ESD_VBUS: D2.2 (A), J3.1 (VBUS), U6.4
GND: C1.1, C2.2, C3.2, C4.2, C5.1, C6.2, C7.2, C8.1, C9.1, C10.2, C11.2, C12.2, C13.2, C14.1, C15.2, C16.1, D1.1 (VSS), D3.1 (K), J2.4 (GND), J3.5 (GND), R7.1, SW1.1, SW2.1, SW3.1, SW4.1, U1.1 (GND), U1.40 (GND), U1.41 (GND), U2.2 (GND), U3.2 (GND), U3.25 (GND), U4.3 (GND), U5.H204 (GND), U5.H209 (PORTSEL), U5.H210 (BR2), U5.H213 (BR1), U6.1, U6.8
unnamed: C4.1, SW4.2, U1.18 (GPIO10/TOUCH10/ADC1_CH9/FSPICS0/FSPIIO4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)
unnamed: D1.2 (DIN), Q1.3 (D), R1.1
unnamed: D3.2 (A), R12.1
unnamed: J1.R, R11.1
unnamed: Q1.2 (S), R2.2, R3.1
unnamed: Q2.1 (B), R5.2
unnamed: Q2.2 (E), R8.1, U3.23 (~DTR)
unnamed: Q3.1 (B), R8.2
unnamed: Q3.2 (E), R5.1, U3.19 (~RTS)
unnamed: R2.1, U1.25 (GPIO48/SPICLK_N/SUBSPICLK_N_DIFF)
unnamed: R9.2, U1.12 (GPIO8/TOUCH8/ADC1_CH7/SUBSPICS1)
unnamed: R11.2, U1.22 (GPIO14/TOUCH14/ADC2_CH3/FSPIWP/FSPIDQS/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)
unnamed: R6.2, U3.9 (~RST)
unnamed: R7.2, R10.2, U3.8 (VBUS)
S4_EN: R9.1, U4.1 (EN)
S4_VBUS: C16.2, J2.1 (VBUS), U4.6 (OUT), U4.8 (OUT), U6.5
U0_RXD: U1.36 (U0RXD/GPIO44/CLK_OUT2), U3.21 (TXD)
U0_TXD: U1.37 (U0TXD/GPIO43/CLK_OUT1), U3.20 (RXD)
VBUS: C1.2, C9.2, C14.2, C15.1, D1.3 (VDD), D2.1 (K), R1.2, R10.1, U2.1 (VI), U4.7 (IN)

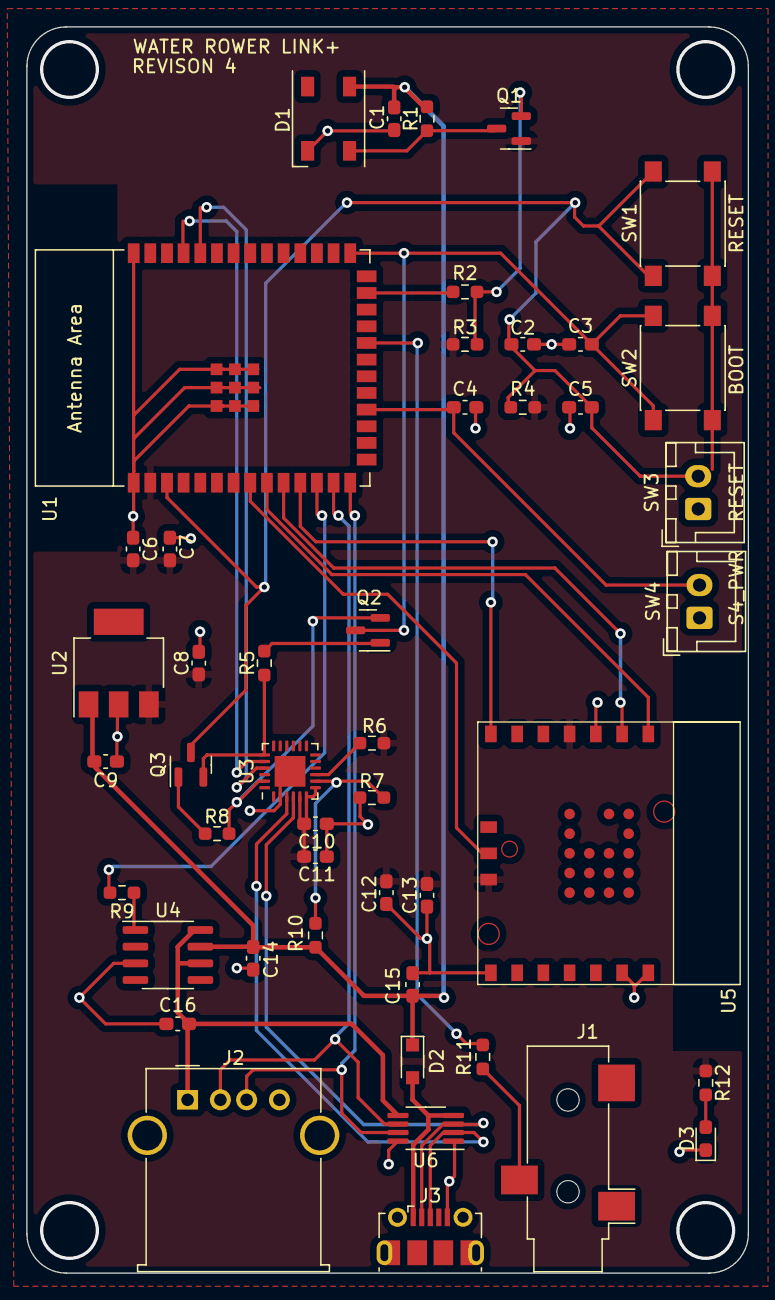
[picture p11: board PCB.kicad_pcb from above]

Board: 2 copper layers, 55.0 x 95.0 mm, 47 parts (0 on the bottom side), 32 nets.

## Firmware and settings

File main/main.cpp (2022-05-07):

/*
   This example code is in the Public Domain (or CC0 licensed, at your option.)

   Unless required by applicable law or agreed to in writing, this
   software is distributed on an "AS IS" BASIS, WITHOUT WARRANTIES OR
   CONDITIONS OF ANY KIND, either express or implied.
*/

/****************************************************************************
*
* This demo showcases creating a GATT database using a predefined attribute table.
* It acts as a GATT server and can send adv data, be connected by client.
* Run the gatt_client demo, the client demo will automatically connect to the gatt_server_service_table demo.
* Client demo will enable GATT server's notify after connection. The two devices will then exchange
* data.
*
****************************************************************************/


#include "freertos/FreeRTOS.h"
#include "freertos/task.h"
#include "freertos/event_groups.h"
#include "esp_system.h"
#include "esp_log.h"
#include "nvs_flash.h"
#include "esp_bt.h"

#include "esp_gap_ble_api.h"
#include "esp_gatts_api.h"
#include "esp_bt_main.h"
#include "esp_gatt_common_api.h"
#include "main.h"

#define WATERROWER_TAG "WATERROWER"

#define PROFILE_NUM                 1
#define PROFILE_APP_IDX             0
#define WATERROWER_APP_ID           0x55
//#define BIKE_APP_ID                 0x57
//#define HR_APP_ID                   0x58
#define WATERROWER_DEVICE_NAME      "WaterRowerLink+"
#define CSC_SVC_INST_ID             0
#define FTMS_SVC_INST_ID            1
#define HR_SVC_INST_ID              2

/* The max length of characteristic value. When the GATT client performs a write or prepare write operation,
*  the data length must be less than GATTS_DEMO_CHAR_VAL_LEN_MAX.
*/
#define GATTS_DEMO_CHAR_VAL_LEN_MAX 500
#define PREPARE_BUF_MAX_SIZE        1024
#define CHAR_DECLARATION_SIZE       (sizeof(uint8_t))

#define ADV_CONFIG_FLAG             (1 << 0)
#define SCAN_RSP_CONFIG_FLAG        (1 << 1)

static uint8_t adv_config_done = 0;

uint16_t csc_handle_table[CSC_IDX_NB];
uint16_t ftms_handle_table[FTMS_IDX_NB];
uint16_t hr_handle_table[HR_IDX_NB];

typedef struct
{
    uint8_t* prepare_buf;
    int                     prepare_len;
} prepare_type_env_t;

static prepare_type_env_t prepare_write_env;

static uint8_t raw_adv_data[] = {
    /* flags */
    0x02, 0x01, 0x06,
    /* tx power*/
    //0x02, 0x0a, 0xeb,
    /* service uuid */
    0x07, 0x03, 0x16, 0x18, 0x0d, 0x18, 0x26, 0x18,
    /* device name */
    0x05, 0x09, 'W', 'R', 'L', '+', 
    /* ftms service data rower+indoor bike*/
    0x06, 0x16, 0x26, 0x18, 0x01, 0b00001100, 0b00000000,
    /* manufactuer data */
    0x05, 0xff,0xff, 0xff, 0x77, 0x72
};

static uint8_t raw_scan_rsp_data[] = {
    /* flags */
    0x02, 0x01, 0x06,
    /* tx power */
    0x02, 0x0a, 0xeb,
    /* service uuid */
    //0x05, 0x03, 0x16, 0x18, 0x0d, 0x18
    //0x0f, 0x09, 'W', 'a', 't', 'e', 'r', 'R', 'o', 'w', 'e', 'r', 'L', 'i', 'n', 'k', '+', 
};

static esp_ble_adv_params_t adv_params = {
    .adv_int_min = 0x20,
    .adv_int_max = 0x40,
    .adv_type = ADV_TYPE_IND,
    .own_addr_type = BLE_ADDR_TYPE_PUBLIC,
    .channel_map = ADV_CHNL_ALL,
    .adv_filter_policy = ADV_FILTER_ALLOW_SCAN_ANY_CON_ANY,
};

struct gatts_profile_inst
{
    esp_gatts_cb_t gatts_cb;
    uint16_t gatts_if;
    uint16_t app_id;
    uint16_t conn_id;
    uint16_t service_handle;
    esp_gatt_srvc_id_t service_id;
    uint16_t char_handle;
    esp_bt_uuid_t char_uuid;
    esp_gatt_perm_t perm;
    esp_gatt_char_prop_t property;
    uint16_t descr_handle;
    esp_bt_uuid_t descr_uuid;
};

static void gatts_profile_event_handler(esp_gatts_cb_event_t event,
    esp_gatt_if_t gatts_if, esp_ble_gatts_cb_param_t* param);

#if 0
/* One gatt-based profile one app_id and one gatts_if, this array will store the gatts_if returned by ESP_GATTS_REG_EVT */
static struct gatts_profile_inst csc_profile_tab[PROFILE_NUM] = {
    [PROFILE_APP_IDX] = {
        .gatts_cb = gatts_profile_event_handler,
        .gatts_if = ESP_GATT_IF_NONE,       /* Not get the gatt_if, so initial is ESP_GATT_IF_NONE */
    },
};
#endif

static const uint16_t cycling_speed_cadence_svc_uuid = ESP_GATT_UUID_CYCLING_SPEED_CADENCE_SVC;
static const uint16_t csc_measurement_uuid = ESP_GATT_UUID_CSC_MEASUREMENT;
static const uint16_t csc_feature_uuid = ESP_GATT_UUID_CSC_FEATURE;
static const uint16_t sensor_location_uuid = ESP_GATT_UUID_SENSOR_LOCATION;
static const uint16_t sc_control_point_uuid = ESP_GATT_UUID_SC_CONTROL_POINT;

static const uint16_t hr_svc_uuid = ESP_GATT_UUID_HEART_RATE_SVC;
static const uint16_t hr_measurement_uuid = ESP_GATT_HEART_RATE_MEAS;
static const uint16_t body_sensor_location_uuid = ESP_GATT_BODY_SENSOR_LOCATION;
static const uint16_t hr_control_point_uuid = ESP_GATT_HEART_RATE_CNTL_POINT;

static const uint16_t ftms_svc_uuid = 0x1826;
static const uint16_t ftms_feature_uuid = 0x2acc;
static const uint16_t ftms_rower_data_uuid = 0x2ad1;
static const uint16_t ftms_indoor_bike_data_uuid = 0x2ad2;
static const uint16_t ftms_control_point_uuid = 0x2ad9;

static const uint16_t primary_service_uuid = ESP_GATT_UUID_PRI_SERVICE;
static const uint16_t character_declaration_uuid = ESP_GATT_UUID_CHAR_DECLARE;
static const uint16_t character_client_config_uuid = ESP_GATT_UUID_CHAR_CLIENT_CONFIG;

static const uint8_t char_prop_read = ESP_GATT_CHAR_PROP_BIT_READ;
static const uint8_t char_prop_write = ESP_GATT_CHAR_PROP_BIT_WRITE;
//static const uint8_t char_prop_read_write_notify   = ESP_GATT_CHAR_PROP_BIT_WRITE | ESP_GATT_CHAR_PROP_BIT_READ | ESP_GATT_CHAR_PROP_BIT_NOTIFY;
static const uint8_t char_prop_notify = ESP_GATT_CHAR_PROP_BIT_NOTIFY;

static uint8_t csc_feature_value[2] = { 0x02, 0x00 };
static uint8_t csc_sensor_location_value[1] = { 0x05 };
//static uint8_t sc_control_point_value[1] = { 0x00 };
static const uint8_t csc_measurement_ccc[2] = { 0x00, 0x00 };
//static const uint8_t csc_sc_control_point_ccc[2] = { 0x00, 0x00 };

static const uint8_t hr_measurement_ccc[2] = { 0x00, 0x00 };
static const uint8_t hr_body_sensor_location_value[1] = { 0x00 };
//static const uint8_t hr_control_point_value[1] = { 0x00 };

static const uint8_t ftms_rower_data_ccc[2] = { 0x00, 0x00 };
                                                                      
static const uint8_t ftms_feature_value[8] = 
{
    0b00100110, 0b01010110, 0b00000000, 0b00000000, 
    0b00000000, 0b00000000, 0b00000000, 0b00000000, 
};


static const esp_gatts_attr_db_t gatt_ftms_db[FTMS_IDX_NB] =
{
    // FTMS Service
    [IDX_FTMS_SVC] = {{ESP_GATT_AUTO_RSP}, {ESP_UUID_LEN_16, (uint8_t*)&primary_service_uuid, ESP_GATT_PERM_READ,
        sizeof(uint16_t), sizeof(hr_svc_uuid), (uint8_t*)&ftms_svc_uuid}},

    /// FTMS Feature
    [IDX_FTMS_FEATURE] =
        {{ESP_GATT_AUTO_RSP}, {ESP_UUID_LEN_16, (uint8_t*)&character_declaration_uuid, ESP_GATT_PERM_READ,
        CHAR_DECLARATION_SIZE, CHAR_DECLARATION_SIZE, (uint8_t*)&char_prop_read}},

    // FTMS Feature Value
    [IDX_FTMS_FEATURE_VAL] =
        {{ESP_GATT_AUTO_RSP}, {ESP_UUID_LEN_16, (uint8_t*)&ftms_feature_uuid, ESP_GATT_PERM_READ,
        GATTS_DEMO_CHAR_VAL_LEN_MAX, sizeof(ftms_feature_value), (uint8_t*)ftms_feature_value}},

    // Rower Data
    [IDX_FTMS_ROWER_DATA] =
        {{ESP_GATT_AUTO_RSP}, {ESP_UUID_LEN_16, (uint8_t*)&character_declaration_uuid, ESP_GATT_PERM_READ,
        CHAR_DECLARATION_SIZE, CHAR_DECLARATION_SIZE, (uint8_t*)&char_prop_notify}},

    // Rower Data Value
    [IDX_FTMS_ROWER_DATA_VAL] =
        {{ESP_GATT_RSP_BY_APP}, {ESP_UUID_LEN_16, (uint8_t*)&ftms_rower_data_uuid, 0,
        sizeof(uint16_t), 0, NULL}},

    // Rower Data Config
    [IDX_FTMS_ROWER_DATA_CFG] =
        {{ESP_GATT_AUTO_RSP}, {ESP_UUID_LEN_16, (uint8_t*)&character_client_config_uuid, ESP_GATT_PERM_READ | ESP_GATT_PERM_WRITE,
        sizeof(uint16_t), sizeof(ftms_rower_data_ccc), (uint8_t*)ftms_rower_data_ccc}},

    // FTMS Control Point
    [IDX_FTMS_CONTROL_POINT] =
        {{ESP_GATT_AUTO_RSP}, {ESP_UUID_LEN_16, (uint8_t*)&character_declaration_uuid, ESP_GATT_PERM_READ,
        CHAR_DECLARATION_SIZE, CHAR_DECLARATION_SIZE, (uint8_t*)&char_prop_write}},

    // FTMS Control Point Value
    [IDX_FTMS_CONTROL_POINT_VAL] =
        {{ESP_GATT_RSP_BY_APP}, {ESP_UUID_LEN_16, (uint8_t*)&ftms_control_point_uuid, ESP_GATT_PERM_WRITE,
        GATTS_DEMO_CHAR_VAL_LEN_MAX, 0, NULL}},

};

static const esp_gatts_attr_db_t gatt_csc_db[CSC_IDX_NB] =
{
    // CSC Service
    [IDX_CSC_SVC] = {{ESP_GATT_AUTO_RSP}, {ESP_UUID_LEN_16, (uint8_t*)&primary_service_uuid, ESP_GATT_PERM_READ,
        sizeof(uint16_t), sizeof(cycling_speed_cadence_svc_uuid), (uint8_t*)&cycling_speed_cadence_svc_uuid}},

        // CSC Measurement
    [IDX_CSC_MEASUREMENT] =
        {{ESP_GATT_AUTO_RSP}, {ESP_UUID_LEN_16, (uint8_t*)&character_declaration_uuid, ESP_GATT_PERM_READ | ESP_GATT_PERM_WRITE,
        CHAR_DECLARATION_SIZE, CHAR_DECLARATION_SIZE, (uint8_t*)&char_prop_notify}},

    // CSC Measurement Value
    [IDX_CSC_MEASUREMENT_VAL] =
        {{ESP_GATT_RSP_BY_APP}, {ESP_UUID_LEN_16, (uint8_t*)&csc_measurement_uuid, 0,
        GATTS_DEMO_CHAR_VAL_LEN_MAX, 0, NULL}},

    // CSC Measurement Config
    [IDX_CSC_MEASUREMENT_CFG] =
        {{ESP_GATT_AUTO_RSP}, {ESP_UUID_LEN_16, (uint8_t*)&character_client_config_uuid, ESP_GATT_PERM_READ | ESP_GATT_PERM_WRITE,
        sizeof(uint16_t), sizeof(csc_measurement_ccc), (uint8_t*)csc_measurement_ccc}},

    /// CSC Feature
    [IDX_CSC_FEATURE] =
        {{ESP_GATT_AUTO_RSP}, {ESP_UUID_LEN_16, (uint8_t*)&character_declaration_uuid, ESP_GATT_PERM_READ,
        CHAR_DECLARATION_SIZE, CHAR_DECLARATION_SIZE, (uint8_t*)&char_prop_read}},

    // CSC Feature Value
    [IDX_CSC_FEATURE_VAL] =
        {{ESP_GATT_AUTO_RSP}, {ESP_UUID_LEN_16, (uint8_t*)&csc_feature_uuid, ESP_GATT_PERM_READ,
        GATTS_DEMO_CHAR_VAL_LEN_MAX, sizeof(csc_feature_value), (uint8_t*)csc_feature_value}},

    // Sensor Location
    [IDX_SENSOR_LOCATION] =
        {{ESP_GATT_AUTO_RSP}, {ESP_UUID_LEN_16, (uint8_t*)&character_declaration_uuid, ESP_GATT_PERM_READ,
        CHAR_DECLARATION_SIZE, CHAR_DECLARATION_SIZE, (uint8_t*)&char_prop_read}},

    // Sensor Location Value
    [IDX_SENSOR_LOCATION_VAL] =
        {{ESP_GATT_AUTO_RSP}, {ESP_UUID_LEN_16, (uint8_t*)&sensor_location_uuid, ESP_GATT_PERM_READ,
        GATTS_DEMO_CHAR_VAL_LEN_MAX, sizeof(csc_sensor_location_value), (uint8_t*)csc_sensor_location_value}},

    // SC Control Point
    [IDX_CSC_SC_CONTROL_POINT] =
        {{ESP_GATT_AUTO_RSP}, {ESP_UUID_LEN_16, (uint8_t*)&character_declaration_uuid, ESP_GATT_PERM_READ,
        CHAR_DECLARATION_SIZE, CHAR_DECLARATION_SIZE, (uint8_t*)&char_prop_write}},

    // SC Control Point Value
    [IDX_CSC_SC_CONTROL_POINT_VAL] =
        {{ESP_GATT_RSP_BY_APP}, {ESP_UUID_LEN_16, (uint8_t*)&sc_control_point_uuid, ESP_GATT_PERM_WRITE,
        GATTS_DEMO_CHAR_VAL_LEN_MAX, 0, NULL}},
};

static const esp_gatts_attr_db_t gatt_hr_db[HR_IDX_NB] =
{
    // HR Service
    [IDX_HR_SVC] = {{ESP_GATT_AUTO_RSP}, {ESP_UUID_LEN_16, (uint8_t*)&primary_service_uuid, ESP_GATT_PERM_READ,
        sizeof(uint16_t), sizeof(hr_svc_uuid), (uint8_t*)&hr_svc_uuid}},

    // HR Measurement
    [IDX_HR_MEASUREMENT] =
        {{ESP_GATT_AUTO_RSP}, {ESP_UUID_LEN_16, (uint8_t*)&character_declaration_uuid, ESP_GATT_PERM_READ,
        CHAR_DECLARATION_SIZE, CHAR_DECLARATION_SIZE, (uint8_t*)&char_prop_notify}},

    // HR Measurement Value
    [IDX_HR_MEASUREMENT_VAL] =
        {{ESP_GATT_RSP_BY_APP}, {ESP_UUID_LEN_16, (uint8_t*)&hr_measurement_uuid, 0,
        sizeof(uint16_t), 0, NULL}},

    // HR Measurement Config
    [IDX_HR_MEASUREMENT_CFG] =
        {{ESP_GATT_AUTO_RSP}, {ESP_UUID_LEN_16, (uint8_t*)&character_client_config_uuid, ESP_GATT_PERM_READ | ESP_GATT_PERM_WRITE,
        sizeof(uint16_t), sizeof(hr_measurement_ccc), (uint8_t*)hr_measurement_ccc}},

    // Body Sensor Location
    [IDX_BODY_SENSOR_LOCATION] =
        {{ESP_GATT_AUTO_RSP}, {ESP_UUID_LEN_16, (uint8_t*)&character_declaration_uuid, ESP_GATT_PERM_READ,
        CHAR_DECLARATION_SIZE, CHAR_DECLARATION_SIZE, (uint8_t*)&char_prop_read}},

    // Body Sensor Location Value
    [IDX_BODY_SENSOR_LOCATION_VAL] =
        {{ESP_GATT_AUTO_RSP}, {ESP_UUID_LEN_16, (uint8_t*)&body_sensor_location_uuid, ESP_GATT_PERM_READ,
        GATTS_DEMO_CHAR_VAL_LEN_MAX, sizeof(hr_body_sensor_location_value), (uint8_t*)hr_body_sensor_location_value}},

    // HR Control Point
    [IDX_HR_CONTROL_POINT] =
        {{ESP_GATT_AUTO_RSP}, {ESP_UUID_LEN_16, (uint8_t*)&character_declaration_uuid, ESP_GATT_PERM_READ,
        CHAR_DECLARATION_SIZE, CHAR_DECLARATION_SIZE, (uint8_t*)&char_prop_write}},

    // HR Control Point Value
    [IDX_HR_CONTROL_POINT_VAL] =
        {{ESP_GATT_RSP_BY_APP}, {ESP_UUID_LEN_16, (uint8_t*)&hr_control_point_uuid, ESP_GATT_PERM_WRITE,
        GATTS_DEMO_CHAR_VAL_LEN_MAX, 0, NULL}},
};

static void gap_event_handler(esp_gap_ble_cb_event_t event, esp_ble_gap_cb_param_t* param)
{
    switch (event)
    {
        case ESP_GAP_BLE_ADV_DATA_RAW_SET_COMPLETE_EVT:
            adv_config_done &= (~ADV_CONFIG_FLAG);
            if (adv_config_done == 0)
            {
                esp_ble_gap_start_advertising(&adv_params);
            }
            break;
        // case ESP_GAP_BLE_SCAN_RSP_DATA_RAW_SET_COMPLETE_EVT:
        //     adv_config_done &= (~SCAN_RSP_CONFIG_FLAG);
        //     if (adv_config_done == 0)
        //     {
        //         esp_ble_gap_start_advertising(&adv_params);
        //     }
        //     break;
        case ESP_GAP_BLE_ADV_START_COMPLETE_EVT:
            /* advertising start complete event to indicate advertising start successfully or failed */
            if (param->adv_start_cmpl.status != ESP_BT_STATUS_SUCCESS)
            {
                ESP_LOGE(WATERROWER_TAG, "advertising start failed");
            }
            else
            {
                ESP_LOGI(WATERROWER_TAG, "advertising start successfully");
            }
            break;
        case ESP_GAP_BLE_ADV_STOP_COMPLETE_EVT:
            if (param->adv_stop_cmpl.status != ESP_BT_STATUS_SUCCESS)
            {
                ESP_LOGE(WATERROWER_TAG, "Advertising stop failed");
            }
            else
            {
                ESP_LOGI(WATERROWER_TAG, "Stop adv successfully\n");
            }
            break;
        case ESP_GAP_BLE_UPDATE_CONN_PARAMS_EVT:
            ESP_LOGI(WATERROWER_TAG, "update connection params status = %d, min_int = %d, max_int = %d,conn_int = %d,latency = %d, timeout = %d",
                param->update_conn_params.status,
                param->update_conn_params.min_int,
                param->update_conn_params.max_int,
                param->update_conn_params.conn_int,
                param->update_conn_params.latency,
                param->update_conn_params.timeout);
            break;
        default:
            break;
    }
}

void example_prepare_write_event_env(esp_gatt_if_t gatts_if, prepare_type_env_t* prepare_write_env, esp_ble_gatts_cb_param_t* param)
{
    ESP_LOGI(WATERROWER_TAG, "prepare write, handle = %d, value len = %d", param->write.handle, param->write.len);
    esp_gatt_status_t status = ESP_GATT_OK;
    if (prepare_write_env->prepare_buf == NULL)
    {
        prepare_write_env->prepare_buf = (uint8_t*)malloc(PREPARE_BUF_MAX_SIZE * sizeof(uint8_t));
        prepare_write_env->prepare_len = 0;
        if (prepare_write_env->prepare_buf == NULL)
        {
            ESP_LOGE(WATERROWER_TAG, "%s, Gatt_server prep no mem", __func__);
            status = ESP_GATT_NO_RESOURCES;
        }
    }
    else
    {
        if (param->write.offset > PREPARE_BUF_MAX_SIZE)
        {
            status = ESP_GATT_INVALID_OFFSET;
        }
        else if ((param->write.offset + param->write.len) > PREPARE_BUF_MAX_SIZE)
        {
            status = ESP_GATT_INVALID_ATTR_LEN;
        }
    }
    /*send response when param->write.need_rsp is true */
    if (param->write.need_rsp)
    {
        esp_gatt_rsp_t* gatt_rsp = (esp_gatt_rsp_t*)malloc(sizeof(esp_gatt_rsp_t));
        if (gatt_rsp != NULL)
        {
            gatt_rsp->attr_value.len = param->write.len;
            gatt_rsp->attr_value.handle = param->write.handle;
            gatt_rsp->attr_value.offset = param->write.offset;
            gatt_rsp->attr_value.auth_req = ESP_GATT_AUTH_REQ_NONE;
            memcpy(gatt_rsp->attr_value.value, param->write.value, param->write.len);
            esp_err_t response_err = esp_ble_gatts_send_response(gatts_if, param->write.conn_id, param->write.trans_id, status, gatt_rsp);
            if (response_err != ESP_OK)
            {
                ESP_LOGE(WATERROWER_TAG, "Send response error");
            }
            free(gatt_rsp);
        }
        else
        {
            ESP_LOGE(WATERROWER_TAG, "%s, malloc failed", __func__);
        }
    }
    if (status != ESP_GATT_OK)
    {
        return;
    }
    memcpy(prepare_write_env->prepare_buf + param->write.offset,
        param->write.value,
        param->write.len);
    prepare_write_env->prepare_len += param->write.len;

}

void example_exec_write_event_env(prepare_type_env_t* prepare_write_env, esp_ble_gatts_cb_param_t* param)
{
    if (param->exec_write.exec_write_flag == ESP_GATT_PREP_WRITE_EXEC && prepare_write_env->prepare_buf)
    {
        esp_log_buffer_hex(WATERROWER_TAG, prepare_write_env->prepare_buf, prepare_write_env->prepare_len);
    }
    else
    {
        ESP_LOGI(WATERROWER_TAG, "ESP_GATT_PREP_WRITE_CANCEL");
    }
    if (prepare_write_env->prepare_buf)
    {
        free(prepare_write_env->prepare_buf);
        prepare_write_env->prepare_buf = NULL;
    }
    prepare_write_env->prepare_len = 0;
}

// #define NOP() asm volatile ("nop")

// void delay(uint32_t ms)
// {
//     vTaskDelay(ms / portTICK_PERIOD_MS);
// }

// void IRAM_ATTR delayMicroseconds(uint32_t us)
// {
//     uint64_t m = (uint64_t)esp_timer_get_time();
//     if (us)
//     {
//         uint64_t e = (m + us);
//         if (m > e)
//         { //overflow
//             while ((uint64_t)esp_timer_get_time() > e)
//             {
//                 NOP();
//             }
//         }
//         while ((uint64_t)esp_timer_get_time() < e)
//         {
//             NOP();
//         }
//     }
// }

void notify_hr_measurement(void* p)
{
    int hr = 60;
    bool increase = true;

    esp_gatt_if_t gatts_if = ((intptr_t)p) >> 16;
    uint16_t conn_id = ((intptr_t)p) & 0xffff;

    for (;;)
    {
        hr += increase ? 1 : -1;
        if (hr < 60 || hr > 200)
        {
            increase = !increase;
        }

        uint8_t hr_measurement_value[2];
        hr_measurement_value[0] = hr >> 8;
        hr_measurement_value[1] = hr & 0xff;

        ESP_LOGI(WATERROWER_TAG, "gatts_if: %u conn_id: %u hr %d", gatts_if, conn_id, hr);
        esp_err_t ret = esp_ble_gatts_send_indicate(gatts_if, conn_id, hr_handle_table[IDX_HR_MEASUREMENT_VAL], sizeof(hr_measurement_value), hr_measurement_value, false);
        if (ret != ESP_OK)
        {
            ESP_LOGI(WATERROWER_TAG, "HR notify error (%d)", ret);
            vTaskDelete(NULL);
        }


        vTaskDelay(1000 / portTICK_PERIOD_MS);
    }
}

#define FTMS_DATA_MORE_DATA       0b0000000000000001
#define FTMS_CADENCE              0b0000000000000010
#define FTMS_TOTAL_DISTANCE       0b0000000000000100
#define FTMS_CURRENT_PACE         0b0000000000001000
#define FTMS_AVG_PACE             0b0000000000010000
#define FTMS_CURRENT_POWER        0b0000000000100000
#define FTMS_AVG_POWER            0b0000000001000000
#define FTMS_RESISTANCE_LEVEL     0b0000000010000000

#define FTMS_EXPENDED_ENERGY      0b0000000100000000
#define FTMS_HEART_RATE           0b0000001000000000
#define FTMS_META_EQU             0b0000010000000000
#define FTMS_ELASPED_TIME         0b0000100000000000
#define FTMS_REMAINING_TIME       0b0001000000000000
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
void app_main(void)
{
    esp_err_t ret = nvs_flash_init();
    if (ret == ESP_ERR_NVS_NO_FREE_PAGES || ret == ESP_ERR_NVS_NEW_VERSION_FOUND)
    {
        ESP_ERROR_CHECK(nvs_flash_erase());
        ESP_ERROR_CHECK(nvs_flash_init());
    }

    ESP_ERROR_CHECK(esp_bt_controller_mem_release(ESP_BT_MODE_CLASSIC_BT));

    esp_bt_controller_config_t bt_cfg = BT_CONTROLLER_INIT_CONFIG_DEFAULT();
    ESP_ERROR_CHECK(esp_bt_controller_init(&bt_cfg));

    ESP_ERROR_CHECK(esp_bt_controller_enable(ESP_BT_MODE_BLE));
    ESP_ERROR_CHECK(esp_bluedroid_init());
    ESP_ERROR_CHECK(esp_bluedroid_enable());
    //ESP_ERROR_CHECK(esp_ble_gatts_register_callback(gatts_event_handler));
    ESP_ERROR_CHECK(esp_ble_gatts_register_callback(gatts_profile_event_handler));
    ESP_ERROR_CHECK(esp_ble_gap_register_callback(gap_event_handler));
    ESP_ERROR_CHECK(esp_ble_gatts_app_register(WATERROWER_APP_ID));
    //ESP_ERROR_CHECK(esp_ble_gatts_app_register(BIKE_APP_ID));
    //ESP_ERROR_CHECK(esp_ble_gatts_app_register(HR_APP_ID));
    ESP_ERROR_CHECK(esp_ble_gatt_set_local_mtu(500));
}

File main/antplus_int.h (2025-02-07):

#define ANTPLUS_INPUT                       0
#define ANTPLUS_OUTPUT                      1
#define ANTPLUS_ANY                         0
#define ANTPLUS_INFINITE_TIMEOUT            255

#define ANTPLUS_MESSAGE_REQUIRED_SIZE(msg)  (sizeof(antplus_message_t) + (msg)->size + 1)
#define ANTPLUS_MESSAGE_SIZE(t)             (sizeof(t) - sizeof(antplus_message_t) - 1)
#define ANTPLUS_MESSAGE(t, id, dir)         { .sync_value = ANTPLUS_SYNC_VALUE, .direction = dir, .size = ANTPLUS_MESSAGE_SIZE(t), .msg_id = id }


#define ANTPLUS_EVENT                       0x01
#define ANTPLUS_BROADCAST                   0x4e
#define ANTPLUS_ACKNOWEDGED_DATA            0x4f
#define ANTPLUS_STARTUP                     0x6f
#define ANTPLUS_REQUEST_MESSAGE             0x4d
#define ANTPLUS_CAPABILITIES                0x54
#define ANTPLUS_VERSION                     0x3e
#define ANTPLUS_CHANNEL_ID                  0x51
#define ANTPLUS_ASSIGN_CHANNEL              0x42
#define ANTPLUS_SET_NETWORK_KEY             0x46
#define ANTPLUS_SET_CHANNEL_RF_FREQ         0x45
#define ANTPLUS_SET_CHANNEL_SEARCH_TIMEOUT  0x44
#define ANTPLUS_SET_CHANNEL_PERIOD          0x43
#define ANTPLUS_SET_CHANNEL_RF_FREQ         0x45
#define ANTPLUS_SET_CHANNEL_TX_POWER        0x60
#define ANTPLUS_OPEN_CHANNEL                0x4b
#define ANTPLUS_CHANNEL_RESPONSE            0x40

#define ANTPLUS_FE_DEVICE_NUM               62282

#define ANTPLUS_UART_BAUD_RATE              115200
#define ANTPLUS_UART_NUM                    UART_NUM_1
#define ANTPLUS_UART_QUEUE_SIZE             10
#define ANTPLUS_MAX_MESSAGE_SIZE            41
#define ANTPLUS_UART_RX_BUFFER_SIZE         1024
#define ANTPLUS_UART_TX_BUFFER_SIZE         0

#define ANTPLUS_CTS_GPIO_NUM                GPIO_NUM_18
#define ANTPLUS_TX_GPIO_NUM                 GPIO_NUM_17
#define ANTPLUS_RX_GPIO_NUM                 GPIO_NUM_16

#define ANTPLUS_RESET_GPIO_NUM              GPIO_NUM_15
#define ANTPLUS_RESET_GPIO_SEL              (1ull << ANTPLUS_RESET_GPIO_NUM)

#define ANTPLUS_SYNC_BYTE_MASK              0xfe
#define ANTPLUS_SYNC_BYTE_VALUE             0xa4
#define ANTPLUS_SYNC_VALUE                  0x52

#define ANTPLUS_PAGE_MASK                   0x7f

#define ANTPLUS_NETWORK_KEY                 { 0xb9, 0xa5, 0x21, 0xfb, 0xbd, 0x72, 0xc3, 0x45 }
#define ANTPLUS_NETWORK_KEY_SIZE            8
#define ANTPLUS_BROADCAST_PAYLOAD_SIZE      8

#define ANTPLUS_PUBLIC_NETWORK              0

#define ANTPLUS_FE                          17
#define ANTPLUS_HRM                         120

#define ANTPLUS_CHANNEL_HRM                 0
#define ANTPLUS_CHANNEL_FE                  1

#define ANTPLUS_0DBM                        3
#define ANTPLUS_2457MHZ                     57

#define ANTPLUS_BIDIRECTIONAL_RECEIVE       0
#define ANTPLUS_BIDIRECTIONAL_TRANSMIT      0x10
#define ANTPLUS_IC                          0x01
#define ANTPLUS_GDP                         0x04


#define ANTPLUS_PAGE_MANUFACTURER_ID        80
#define ANTPLUS_PAGE_PRODUCT_INFO           81
#define ANTPLUS_PAGE_ROWING_DATA            22
#define ANTPLUS_PAGE_GENERAL_FE             16
#define ANTPLUS_ROWER                       22
#define ANTPLUS_CAPS_HR_FE                  0x03
#define ANTPLUS_CAPS_HR_EM                  0x02
#define ANTPLUS_CAPS_HR_ANT                 0x01
#define ANTPLUS_CAPS_DISTANCE               0x04
#define ANTPLUS_CAPS_VIRTUAL_SPEED          0x08
#define ANTPLUS_CAPS_STROKES                0x01

#define ANTPLUS_EVENT_READY                 0x01

typedef struct
{
    uint8_t uart_num;
    QueueHandle_t uart_queue_handle;
    TaskHandle_t recv_task_handle;
    state_manager_handle_t sm_handle;    
    hrm_handle_t hrm_handle;
    s4_handle_t s4_handle;
    EventGroupHandle_t eg_handle;
    portMUX_TYPE mux;
    uint16_t heart_beat_ts;
}
antplus_driver_t;

typedef struct
{
    uint8_t direction : 1;
    uint8_t sync_value : 7;
    uint8_t size;
    uint8_t msg_id;
    uint8_t data[];
}
__attribute__((packed)) antplus_message_t;

typedef struct
{
    uint8_t direction : 1;
    uint8_t sync_value : 7;
    uint8_t size;
    uint8_t msg_id;
    struct
    {
        uint8_t channel;
        uint8_t payload[ANTPLUS_BROADCAST_PAYLOAD_SIZE];
    }
    __attribute__((packed)) data;
    uint8_t checksum;
}
__attribute__((packed)) antplus_broadcast_message_t;

typedef struct
{
    uint8_t direction : 1;
    uint8_t sync_value : 7;
    uint8_t size;
    uint8_t msg_id;
    struct
    {
        uint8_t channel;
        uint8_t page_num : 7;
        uint8_t page_change_toggle : 1;
        union
        {
            struct 
            {
                uint8_t reserved[3];
                uint16_t heart_beat_ts;
                uint8_t heart_beat_count;
                uint8_t hr;
            }
            __attribute__((packed)) common;
        }
        __attribute__((packed));
    }
    __attribute__((packed)) data;
    uint8_t checksum;
}
__attribute__((packed)) antplus_heartrate_broadcast_t;

typedef struct
{
    uint8_t direction : 1;
    uint8_t sync_value : 7;
    uint8_t size;
    uint8_t msg_id;
    struct
    {
        uint8_t channel;
        uint8_t page_num;
        uint8_t reserved0;
        uint8_t reserved1;
        uint8_t hw_revision;
        uint16_t manufacturer_id;
        uint16_t model_no;
    }
    __attribute__((packed)) data;
    uint8_t checksum;
}
__attribute__((packed)) antplus_manufacturer_id_page_t;

typedef struct
{
    uint8_t direction : 1;
    uint8_t sync_value : 7;
    uint8_t size;
    uint8_t msg_id;
    struct
    {
        uint8_t channel;
        uint8_t page_num;
        uint8_t reserved;
        uint8_t sw_rev_supp;
        uint8_t sw_rev_main;
        uint32_t serial_no;
    }
    __attribute__((packed)) data;
    uint8_t checksum;
}
__attribute__((packed)) antplus_product_info_page_t;

typedef struct
{
    uint8_t direction : 1;
    uint8_t sync_value : 7;
    uint8_t size;
    uint8_t msg_id;
    struct
    {
        uint8_t channel;
        uint8_t page_num;
        uint8_t reserved0;
        uint8_t reserved1;
        uint8_t stroke_count;
        uint8_t cadence;
        uint16_t power;
        uint8_t flags;        
    }
    __attribute__((packed)) data;
    uint8_t checksum;
}
__attribute__((packed)) antplus_rowing_data_page_t;

typedef struct
{
    uint8_t direction : 1;
    uint8_t sync_value : 7;
    uint8_t size;
    uint8_t msg_id;
    struct
    {
        uint8_t channel;
        uint8_t page_num;
        uint8_t equipment_type;
        uint8_t elasped;
        uint8_t distance;
        uint16_t speed;
        uint8_t heart_rate;
        uint8_t flags;
    }
    __attribute__((packed)) data;
    uint8_t checksum;
}
__attribute__((packed)) antplus_general_fe_page_t;

typedef struct
{
    uint8_t direction : 1;
    uint8_t sync_value : 7;
    uint8_t size;
    uint8_t msg_id;
    struct
    {
        uint8_t channel;
        uint8_t msg_id;
    }
    __attribute__((packed)) data;
    uint8_t checksum;
}
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

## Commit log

2022-05-07 power tweak
2022-05-07 power button!
2022-05-07 ble bug fixes clean up
    [antplus.c, antplus_int.h, ble_int.h]
2022-05-07 cleanup & fix monitor usb reset error
    [main.c, s4.c, s4_int.h]
2022-05-07 led status
2022-05-07 led tweaks
2022-05-07 device unplug robustness
2022-05-07 prototype schematic
    [proto.kicad_sch]
2022-05-07 pcb tweaks
    [PCB.kicad_pcb]
2022-05-07 ordered pcb
    [PCB-B_Cu.gbr, PCB-B_Paste.gbr, PCB-B_Silkscreen.gbr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]
2022-05-07 swap led part#
    [PCB-B_Cu.gbr, PCB-B_Mask.gbr, PCB-B_Paste.gbr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]
2022-05-07 sync pcb GPIO reboot on crash more error handling
    [Breadboard.kicad_sch]
2022-05-07 board updates
    [PCB.csv, PCB.kicad_pcb, PCB.kicad_sch]
2022-05-07 Revision 2: Fixed auto program transistor pins Fixed TX/RX to U0 Increased board size Added screw holes Added BOOT switch Added RESET jumper
    [PCB-B_Cu.gbr, PCB-B_Mask.gbr, PCB-B_Paste.gbr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]
2022-05-07 moved CP210N via
    [PCB-B_Cu.gbr, PCB-B_Mask.gbr, PCB-B_Paste.gbr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]
2022-05-07 R3 PCB
    [PCB.csv, PCB.kicad_pcb]
2022-05-19 Rev 3: increase screw hole size
    [PCB-B_Cu.gbr, PCB-B_Mask.gbr, PCB-B_Paste.gbr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]
2022-06-09 R4 screw hole clearance
    [PCB-B_Cu.gbr, PCB-B_Mask.gbr, PCB-B_Paste.gbr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]
2022-06-11 Earth to GND
    [PCB.kicad_pcb, PCB.kicad_sch]
2022-07-16 add GND via
    [PCB.csv, PCB.kicad_pcb]
2022-07-19 remove printf
2022-08-16 small tweaks
    [PCB.kicad_pcb]
2022-08-31 fix 3d models
    [PCB.kicad_pcb, PCB.kicad_sch]
2022-08-31 grid origin
    [PCB.kicad_pcb]
2022-08-31 case R1
    [Box.step, Cover.step, WaterRower Link Plus.FCStd]
2022-09-02 final case
    [Box.step, Cover.step, WaterRower Link Plus.FCStd]
2025-02-07 update idf sdk compatibility
    [PCB.kicad_pcb, PCB.kicad_sch]
